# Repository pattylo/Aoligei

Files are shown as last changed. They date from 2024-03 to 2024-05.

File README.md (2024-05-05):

# AIRO-LAB Drone Standardization
## Aoligei-C, Aoligei-V, Aoligei-L

This documentation serves as the tutorial for setting up (from hardware to software) drone **Aoligei**, including -C (for control), -V (for visual), -L (for LiDAR).

## 1. What to buy.
- Follow this [file](/documents/buy_hardware.docx) to buy all the things your need. 
- Use the files [here]() to order 3D models. 

## 2. VIM4 - the on board computer
This document provides detailed guidance of configuring VIM4. We assume that you have
- A VIM4
- A heat sink for VIM4
- A fan for VIM4
- A 512G SD card
- A stable WIFI connection
- A HDMI monitor
- A set of external keyboard and mouse

### 2.1. Install Ubuntu 22.04 to VIM4
1.  Install the heatsink and the fan to VIM4 by following the manual provided in the heatsink package. VIM4 does not work without a heatsink.

2. Insert the SD card into a SD card reader.

3. Download the software from https://docs.khadas.com/products/sbc/vim4/install-os/install-os-into-external-storage, and download “ETCHER FOR WINDOWS (X86|X64) (INSTALLER)”.

4. Download the system image from https://dl.khadas.com/products/vim4/firmware/ubuntu/generic/. Choose “vim4-ubuntu-22.04-gnome-linux-5.15-fenix-1.6-231229.img.xz”.

5. Use the software “balenaEtcher” and the system image downloaded in Step2 to install ubuntu for VIM4.

### 2.2. Post Installation
1. First setup a new username with [NATO-alphabets](https://en.wikipedia.org/wiki/NATO_phonetic_alphabet) (for easy management lah...). Make it administrator to have ```sudo``` power. 
2. Then, reboot, login with new user, and delete the ```khadas``` user. Run the following to change the username:
    ```
    sudo passwd {username}
    ```
3. For convenience, you'd better install Firefox to your VIM4 because Google Chrome is not supported.

`However, YOU MUST NOT USE "snap" to install Firefox since there might be a bug in arm-ubuntu22.04. 
 Therefore, either install Firefox with traditional "apt-get" or do not use Firefox !!`

4. Install docker in VIM4. Follow this [page](https://docs.docker.com/engine/install/ubuntu/) and it should get the task done. Remember to read everything when you are doing the installation, please do not just blindly copy every single command into your terminal.
5. Do the following to get your Docker image:
    ```
    git clone https://github.com/HKPolyU-UAV/airo_docker_lib
    ./build_hehe.sh vimswift
    ```
   After building the image, do:
   ```
   ./run_hehe.sh vimswift
   ```
6. Voila! You have an usable programming environment now! When modifying your code, we suggest you to use VScode on your own laptop and connect the drone with ```ssh```. You can refer to this [documentation](https://github.com/pattylo/useful_tools/blob/main/vscode_github/vscode_github.md) for more info.

## 3. Firmware Setup
- A computer w/ Ubuntu >=20.04
- A Kakute FCU (v1.3 || v2)
- A Type-C USB wire
- A 4G SD card (if you are using Kakute v1.3)

### 3.1. Firmware Upgrade
1. Install DFU library on your own computer
    ```
    sudo apt install dfu-util -y
    ```
2. Erase and load the binary file to the FCU.
    ```
    git clone https://github.com/HKPolyU-UAV/Aoligei.git && cd Aoligei
    ```
    Then, unplug your USB connection, press the DUF button, plug your FCU into your computer, and unpress the DFU button. Then, do:
    ```
    dfu-util -a 0 --dfuse-address 0x08000000:force:mass-erase:leave -D ./build/holybro_kakuteh7_bootloader.bin 
    # ignore the error
    # use "holybro_kakuteh7v2_bootloader" if your are using v2
    ```
    And then, unplug your USB connection, press the DUF button, plug your FCU into your computer, and unpress the DFU button. Now do:
    ```
    dfu-util -a 0 --dfuse-address 0x08000000 -D ./build/holybro_kakuteh7_bootloader.bin
    # again, use "holybro_kakuteh7v2_bootloader" if your are using v2
    ```
3. Load firmware to the FCU. Open QGC, and go to "Firmware" to upload ```.px4``` to FCU. Note that you should tick on "advance settings", and then select "Custom firmware file..." under the drop-down options.

   <div align=center>
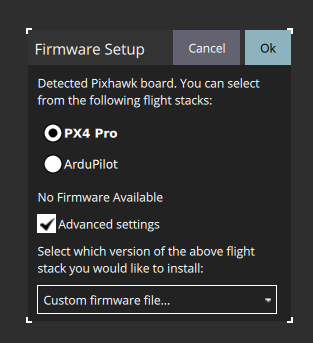
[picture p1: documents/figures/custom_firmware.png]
   
   </div>

    Click "OK", it should pop out a file selection panel. Go the "build" file of this repo, and select [this (v1.3)](/build/holybro_kakuteh7_default.px4) or [that (v2)](/build/holybro_kakuteh7v2_default.px4).

4. If you want to build from source on your own, refer to [this](./documents/fcu.md)

## 4. Pre-configuration of the FCU
### 4.1. Parameter settings
We assume you have at least finished the procedure "C" aforementioned. This part provides some pre-configurations of the FCU. Therefore, we assume you have

- An assembled drone with a FCU, a VIM4, four motors, a battery. (If you still don't know how to install ubuntu22 or docker file into VIM4, never mind. It won't affect this step.)
- QGC in Ubuntu. (Windows would be fine, but Ubuntu is preferred.)
- A type-C cable.

**NOTING: This drone is currently only used in a motion-capture-located in-door room. Out door flight is currently not supported.**

You may need half a minute to connect the FCU with QGC. When the connection is stable, you can see a content on the left of GQC.
Select "Parameters", and the following parameters need to be reset:

| Parameter |  Value | Comment |
|:---:|:---:|:---:|
| SYS_HAS_MAG | 0 |  This FCU does not have a magnetometer  |
| SYS_HAS_GPS | Disabled | This drone does not have a GPS |
| SYS_HAS_BARO | Disabled | This FCU does not have a barometer |
| SYS_MC_EST_GROUP | ekf2 | |
| SDLOG_MODE | disabled | Disable the log file to save CPU memory |

Reboot the FCU with QGC, when the FCU is reloaded, set

| Parameter |  Value | Comment |
|:---:|:---:|:---:|
|  EKF2_EV_CTRL  | 15 | |
|  EKF2_HGT_REF  |  Vision  | |
|  MAV_0_CONFIG  | Disabled | |
|  MAV_1_CONFIG  |  TELEM1  | |
| SER_TEL1_BAUD  |  921600  | |

Reboot the FCU with QGC, and this step is completed.

### 4.2. Quadrotor calibration
Then, we start to calibrate the quadrotor. Noting that different people have different styles.
Therefore, you don't need to follow EVERYTHING. We assume you can connect the FCU with QGC.

#### 4.2.1 Sensors
Calibrate Gyroscope, Accelerator, Level Horizon, and Orientations, respectively.
The "Autopilot Orientation" is "ROTATION_NONE" (default.)

#### 4.2.2. Radio
We need to connect the FASST receiver to the radio. Firstly, open the radio and switch it to FASST mode.
Secondly, push the mode select button on the receiver and then power on the receiver.
Now the light on the receiver is shinning and remains green. Then connection is finished.
We use "Mode2" here, as shown bellow. (If you have your own style, follow you own style.)

<div align=center>
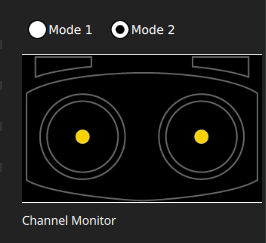
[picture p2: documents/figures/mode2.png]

</div>

Then, calibrate the radio as others do. Nothing special; therefore, detailed description is omitted here.

#### 4.2.3. Flight mode setting
The following is the mode setting of our group. You can have your own style.

<div align=center>
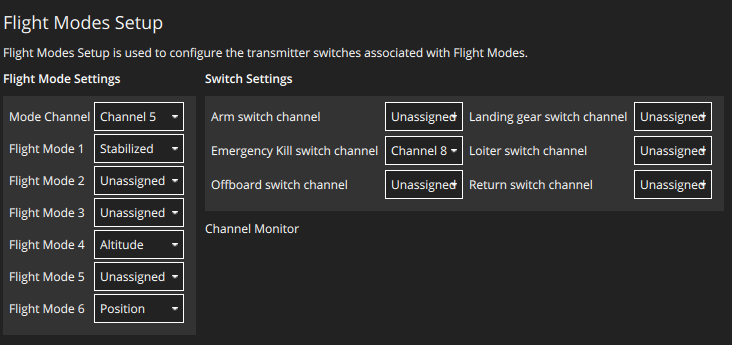
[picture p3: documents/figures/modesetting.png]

</div>

#### 4.2.4. Power setup and ESC calibration
**DO NOT INSTALL PROPELLERS!!**

Connect the drone with the battery. Push the first "Calculate" in the following figure.
Enter the measured voltage of the battery into the blank.
Then, and write the series of your battery (3, 4, or 6) into "Number of Cells"

<div align=center>
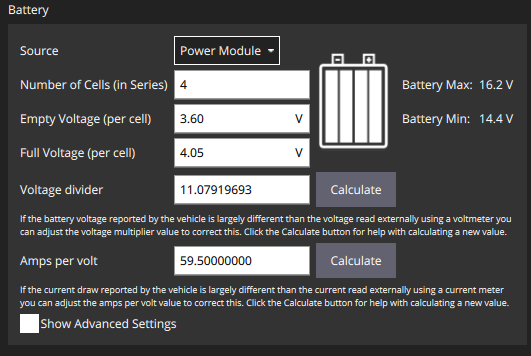
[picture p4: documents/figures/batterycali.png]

</div>

Then, calibrate the ESC. Click the button in the following figure. Just follow the instructions.
<div align=center>
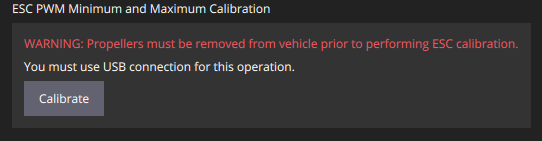
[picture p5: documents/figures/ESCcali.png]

</div>

#### 4.2.5. Calibrate Actuators
Firstly, you should see a screen like this.

<div align=center>
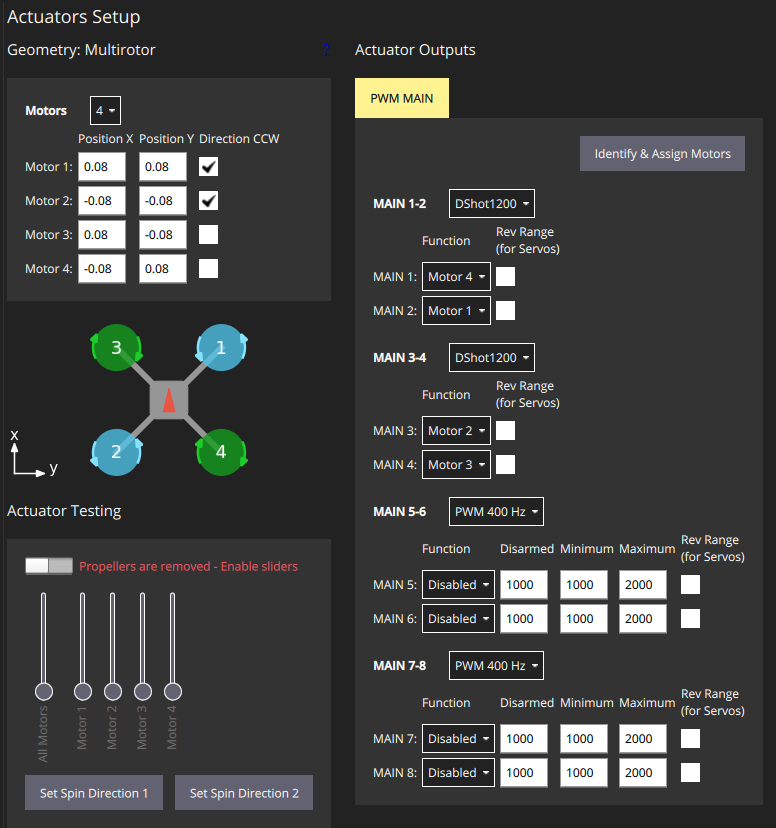
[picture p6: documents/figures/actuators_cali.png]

</div>

See the right column, set the MAIN1-2 and MAIN3-4 to "DShot1200", and then press "Identify & Assign Motors".

Secondly, see the left column, the positions (X and Y) from Motor 1 to 4 are shown below.

|  Motor |  Position X  |  Position Y  |  Direction CCW  |
|:---:|:---:|:---:|:---:|
|  Motor1  | 0.08 | 0.08 | Yes |
|  Motor2  | -0.08 | -0.08 | Yes |
|  Motor3  | 0.08 | -0.08 | No |
|  Motor4  | -0.08 | 0.08 | No |

Noting that the "0.08" here is especially designed for our own drone.
You'd better use a ruler to measure the semi-major axis of your own drone.
Then, the expected rotation direction of the four motors are shown in the QGC.

<div align=center>
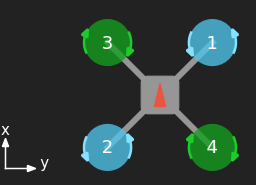
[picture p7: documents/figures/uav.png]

</div>

Finally, you need to reverse the rotation direction if some motors don't rotate as expected.
Use the buttons "Set Spin Direction 1" and "Set Spin Direction 2" to correct them, which are shown below.

<div align=center>
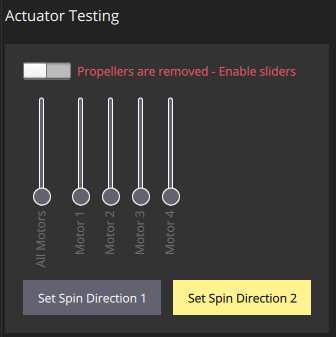
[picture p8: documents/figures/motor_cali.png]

</div>

### 4.3 Post Calibration
Unplug your SD card, connect the SD card to your PC. Create a new folder "etc" to the SD card.
create "extras.txt" in "etc" folder. Then, copy the following items into the txt file.

```
mavlink stream -d /dev/ttyS0 -s LOCAL_POSITION_NED -r 100
mavlink stream -d /dev/ttyS0 -s ATTITUDE_TARGET -r 100
mavlink stream -d /dev/ttyS0 -s BATTERY_STATUS -r 100
```

Congratulations! If everything goes well, you have finished pre-configurations of the drone.

`Tips: Although we provide detailed calibration instruction here,
many users (including ourselves) would meet many confused bugs while doing the step.
That is because different people have totally different styles, use different hardware, have different QGC version, have different radios, et al. 
PLease feel free to ask the "Maintainers" shown below and share us your weired bugs.
We might don't know how to fix your bugs, but we are curious about them. Thank you very much!`

## 5. System Identification 
@ https://github.com/RockyJBL
Please follow the [link](https://github.com/HKPolyU-UAV/airo_control_interface.git) here to conduct the system identification.

## Maintainers
[Yefeng](https://github.com/Yang-Yefeng) @ AIRO-LAB @ RCUAS, HKPolyU <br>
[RockyJBL](https://github.com/RockyJBL) @ AIRO-LAB @ RCUAS, HKPolyU <br>
[VITO](https://github.com/Vitollee) @ AIRO-LAB @ RCUAS, HKPolyU <br>
[pattylo](https://github.com/pattylo) @ AIRO-LAB @ RCUAS, HKPolyU

<!-- # PX4 Drone Autopilot

[![Releases](https://img.shields.io/github/release/PX4/PX4-Autopilot.svg)](https://github.com/PX4/PX4-Autopilot/releases) [![DOI](https://zenodo.org/badge/22634/PX4/PX4-Autopilot.svg)](https://zenodo.org/badge/latestdoi/22634/PX4/PX4-Autopilot)

[![Nuttx Targets](https://github.com/PX4/PX4-Autopilot/workflows/Nuttx%20Targets/badge.svg)](https://github.com/PX4/PX4-Autopilot/actions?query=workflow%3A%22Nuttx+Targets%22?branch=master) [![SITL Tests](https://github.com/PX4/PX4-Autopilot/workflows/SITL%20Tests/badge.svg?branch=master)](https://github.com/PX4/PX4-Autopilot/actions?query=workflow%3A%22SITL+Tests%22)

[![Discord Shield](https://discordapp.com/api/guilds/1022170275984457759/widget.png?style=shield)](https://discord.gg/dronecode)

This repository holds the [PX4](http://px4.io) flight control solution for drones, with the main applications located in the [src/modules](https://github.com/PX4/PX4-Autopilot/tree/main/src/modules) directory. It also contains the PX4 Drone Middleware Platform, which provides drivers and middleware to run drones.

PX4 is highly portable, OS-independent and supports Linux, NuttX and MacOS out of the box.

* Official Website: http://px4.io (License: BSD 3-clause, [LICENSE](https://github.com/PX4/PX4-Autopilot/blob/main/LICENSE))
* [Supported airframes](https://docs.px4.io/main/en/airframes/airframe_reference.html) ([portfolio](https://px4.io/ecosystem/commercial-systems/)):
  * [Multicopters](https://docs.px4.io/main/en/frames_multicopter/)
  * [Fixed wing](https://docs.px4.io/main/en/frames_plane/)
  * [VTOL](https://docs.px4.io/main/en/frames_vtol/)
  * [Autogyro](https://docs.px4.io/main/en/frames_autogyro/)
  * [Rover](https://docs.px4.io/main/en/frames_rover/)
  * many more experimental types (Blimps, Boats, Submarines, High altitud Pe balloons, etc)
* Releases: [Downloads](https://github.com/PX4/PX4-Autopilot/releases)

## Building a PX4 based drone, rover, boat or robot

The [PX4 User Guide](https://docs.px4.io/main/en/) explains how to assemble [supported vehicles](https://docs.px4.io/main/en/airframes/airframe_reference.html) and fly drones with PX4.
See the [forum and chat](https://docs.px4.io/main/en/#getting-help) if you need help!

## Changing code and contributing

This [Developer Guide](https://docs.px4.io/main/en/development/development.html) is for software developers who want to modify the flight stack and middleware (e.g. to add new flight modes), hardware integrators who want to support new flight controller boards and peripherals, and anyone who wants to get PX4 working on a new (unsupported) airframe/vehicle.

Developers should read the [Guide for Contributions](https://docs.px4.io/main/en/contribute/).
See the [forum and chat](https://docs.px4.io/main/en/#getting-help) if you need help!

### Weekly Dev Call

The PX4 Dev Team syncs up on a [weekly dev call](https://docs.px4.io/main/en/contribute/).

> **Note** The dev call is open to all interested developers (not just the core dev team). This is a great opportunity to meet the team and contribute to the ongoing development of the platform. It includes a QA session for newcomers. All regular calls are listed in the [Dronecode calendar](https://www.dronecode.org/calendar/).

## Maintenance Team

Note: This is the source of truth for the active maintainers of PX4 ecosystem.

| Sector | Maintainer |
|---|---|
| Founder | [Lorenz Meier](https://github.com/LorenzMeier) |
| Architecture | [Daniel Agar](https://github.com/dagar) / [Beat Küng](https://github.com/bkueng)|
| State Estimation | [Mathieu Bresciani](https://github.com/bresch) / [Paul Riseborough](https://github.com/priseborough) |
| OS/NuttX | [David Sidrane](https://github.com/davids5) |
| Drivers | [Daniel Agar](https://github.com/dagar) |
| Simulation | [Jaeyoung Lim](https://github.com/Jaeyoung-Lim) |
| ROS2 | [Beniamino Pozzan](https://github.com/beniaminopozzan) |
| Community QnA Call | [Ramon Roche](https://github.com/mrpollo) |
| [Documentation](https://docs.px4.io/main/en/) | [Hamish Willee](https://github.com/hamishwillee) |

| Vehicle Type | Maintainer |
|---|---|
| Multirotor | [Matthias Grob](https://github.com/MaEtUgR) |
| Fixed Wing | [Thomas Stastny](https://github.com/tstastny) |
| Hybrid VTOL | [Silvan Fuhrer](https://github.com/sfuhrer) |
| Boat | x |
| Rover | x |

See also [maintainers list](https://px4.io/community/maintainers/) (px4.io) and the [contributors list](https://github.com/PX4/PX4-Autopilot/graphs/contributors) (Github). However it may be not up to date.

## Supported Hardware

Pixhawk standard boards and proprietary boards are shown below (discontinued boards aren't listed).

For the most up to date information, please visit [PX4 user Guide > Autopilot Hardware](https://docs.px4.io/main/en/flight_controller/).

### Pixhawk Standard Boards

These boards fully comply with Pixhawk Standard, and are maintained by the PX4-Autopilot maintainers and Dronecode team

* FMUv6X and FMUv6C
  * [CUAV Pixahwk V6X (FMUv6X)](https://docs.px4.io/main/en/flight_controller/cuav_pixhawk_v6x.html)
  * [Holybro Pixhawk 6X (FMUv6X)](https://docs.px4.io/main/en/flight_controller/pixhawk6x.html)
  * [Holybro Pixhawk 6C (FMUv6C)](https://docs.px4.io/main/en/flight_controller/pixhawk6c.html)
  * [Holybro Pix32 v6 (FMUv6C)](https://docs.px4.io/main/en/flight_controller/holybro_pix32_v6.html)
* FMUv5 and FMUv5X (STM32F7, 2019/20)
  * [Pixhawk 4 (FMUv5)](https://docs.px4.io/main/en/flight_controller/pixhawk4.html)
  * [Pixhawk 4 mini (FMUv5)](https://docs.px4.io/main/en/flight_controller/pixhawk4_mini.html)
  * [CUAV V5+ (FMUv5)](https://docs.px4.io/main/en/flight_controller/cuav_v5_plus.html)
  * [CUAV V5 nano (FMUv5)](https://docs.px4.io/main/en/flight_controller/cuav_v5_nano.html)
  * [Auterion Skynode (FMUv5X)](https://docs.auterion.com/avionics/skynode)
* FMUv4 (STM32F4, 2015)
  * [Pixracer](https://docs.px4.io/main/en/flight_controller/pixracer.html)
  * [Pixhawk 3 Pro](https://docs.px4.io/main/en/flight_controller/pixhawk3_pro.html)
* FMUv3 (STM32F4, 2014)
  * [Pixhawk 2](https://docs.px4.io/main/en/flight_controller/pixhawk-2.html)
  * [Pixhawk Mini](https://docs.px4.io/main/en/flight_controller/pixhawk_mini.html)
  * [CUAV Pixhack v3](https://docs.px4.io/main/en/flight_controller/pixhack_v3.html)
* FMUv2 (STM32F4, 2013)
  * [Pixhawk](https://docs.px4.io/main/en/flight_controller/pixhawk.html)

### Manufacturer supported

These boards are maintained to be compatible with PX4-Autopilot by the Manufacturers.

* [ARK Electronics ARKV6X](https://docs.px4.io/main/en/flight_controller/arkv6x.html)
* [CubePilot Cube Orange+](https://docs.px4.io/main/en/flight_controller/cubepilot_cube_orangeplus.html)
* [CubePilot Cube Orange](https://docs.px4.io/main/en/flight_controller/cubepilot_cube_orange.html)
* [CubePilot Cube Yellow](https://docs.px4.io/main/en/flight_controller/cubepilot_cube_yellow.html)
* [Holybro Durandal](https://docs.px4.io/main/en/flight_controller/durandal.html)
* [Airmind MindPX V2.8](http://www.mindpx.net/assets/accessories/UserGuide_MindPX.pdf)
* [Airmind MindRacer V1.2](http://mindpx.net/assets/accessories/mindracer_user_guide_v1.2.pdf)
* [Holybro Kakute F7](https://docs.px4.io/main/en/flight_controller/kakutef7.html)

### Community supported

These boards don't fully comply industry standards, and thus is solely maintained by the PX4 public community members.

### Experimental

These boards are nor maintained by PX4 team nor Manufacturer, and is not guaranteed to be compatible with up to date PX4 releases.

* [Raspberry PI with Navio 2](https://docs.px4.io/main/en/flight_controller/raspberry_pi_navio2.html)
* [Bitcraze Crazyflie 2.0](https://docs.px4.io/main/en/complete_vehicles/crazyflie2.html)

## Project Roadmap

**Note: Outdated**

A high level project roadmap is available [here](https://github.com/orgs/PX4/projects/25).

## Project Governance

The PX4 Autopilot project including all of its trademarks is hosted under [Dronecode](https://www.dronecode.org/), part of the Linux Foundation.

<a href="https://www.dronecode.org/" style="padding:20px" ><img src="https://mavlink.io/assets/site/logo_dronecode.png" alt="Dronecode Logo" width="110px"/></a>
<a href="https://www.linuxfoundation.org/projects" style="padding:20px;"><img src="https://mavlink.io/assets/site/logo_linux_foundation.png" alt="Linux Foundation Logo" width="80px" /></a>
<div style="padding:10px">&nbsp;</div> -->

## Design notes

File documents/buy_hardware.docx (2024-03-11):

物品 | 数量 | 链接 | 备注 | 价格 (大约\RMB)
飞控板 (电调) | 1个 | 【淘宝】https://m.tb.cn/h.5ve4uwALOcqdL18?tk=eCySWmf9DYx CZ0012 「Holybro Kakute H7 V1.3 飞控 F7 大疆 模拟 航模 蓝牙」 点击链接直接打开 或者 淘宝搜索直接打开 | H7 V1.3+Tekko32 F4 4in1 50A ESC | 1100
飞控板SD卡 | 1张 | 【淘宝】https://m.tb.cn/h.5ECz1sldd7Osilm?tk=vJC2Wmf7vUz CZ8908 「sandisk闪迪tf卡4g手机内存卡class4存储卡micro sd卡小音箱 小卡」 点击链接直接打开 或者 淘宝搜索直接打开 | 4G | 30
板载计算机 | 1台 | 【淘宝】https://m.tb.cn/h.5vIIDjsSOScYAkE?tk=z8ViWmfkVCp CZ0002 「khadas VIM4 Amlogic A311D2 开发板Mali G52 MP8(8EE) GPU」 点击链接直接打开 或者 淘宝搜索直接打开 | Khadas VIM4 + 散热器 + 风扇 | 1650
板载计算机SD卡 | 1张 | 【淘宝】https://m.tb.cn/h.5ve4uzfCTN9hk0G?tk=zud9Wmf9DXo CZ8908 「三星TF卡512G存储卡手机电脑平板摄像头记录仪无人机switch内存卡」 点击链接直接打开 或者 淘宝搜索直接打开 | 512G PRO Plus | 350
航模电机 | 4个 | 【淘宝】https://m.tb.cn/h.5ve4F0b5MVgFCnf?tk=xtZvWmf7v6d CA6496 「T-Motor 乘风 Velox V2306 V2207 V2 电机 5寸 4S 6S 马达」 点击链接直接打开 或者 淘宝搜索直接打开 | V2207 KV1750 (V3.0) | 300 (4个)
电池 | 1块 | 【淘宝】https://m.tb.cn/h.5ve4uzAfdkGmNAv?tk=uTMPWmf9DXz HU9046 「ACE格氏4S电池 航模 5300 4000 3300 2600 2200MAH 格式14.8V锂电」 点击链接直接打开 或者 淘宝搜索直接打开 | 4S 2700 mAh，如果没有，2400mAh或者3300mAh也行 | 300
机架 | 1套 | 无 | 李凡一1.0 | 200
FASST 接收机 | 1个 | 【淘宝】https://m.tb.cn/h.5EyjOM2?tk=CumVWmf5fD0 CZ0000 「X-BOSS FM900接收机 RSSI输出 FASST协议 穿越机SBUS/FUTABA/2.4G」 点击链接直接打开 或者 淘宝搜索直接打开 | FASST | 90
航模遥控器 | 1个 | 【淘宝】https://m.tb.cn/h.5vVZYqGZzLXjnPT?tk=mNvEWmU8Bd0 CZ0001 「FUTABA T16IZS SUPER 香槟金版本18通遥控器中文菜单16IZ升级」 点击链接直接打开 或者 淘宝搜索直接打开 | 左手油门/美国手 | 3200
升压模块 | 1个 | 【淘宝】https://m.tb.cn/h.5EeQpN7h2WZBn2v?tk=xdZbWmfUERN CZ3458 「DC-DC升压模块 SX1308可调升压模块/2A升压板 带MICRO/2A升压板」 点击链接直接打开 或者 淘宝搜索直接打开 | 看好升压范围，输出能囊括12-20V即可 | 3
USB转串口TTL | 1个 | 【淘宝】https://m.tb.cn/h.5w9Yb4wYnox8S4l?tk=wyDZWmHhYEv MF1643 「CP2102模块USB转TTL升级板UBS转串口STC单片机下载刷机六合一UART」 点击链接直接打开 或者 淘宝搜索直接打开 | CP2102版 | 25
螺旋桨 | 1套 | 【淘宝】https://m.tb.cn/h.5ECJTSyQdFe4Gub?tk=SixTWmf7vgv CZ0001 「乾丰MCK 51466V2 5寸穿越机FPV竞速桨叶 51466V2 5寸竞速螺旋桨」 点击链接直接打开 或者 淘宝搜索直接打开 | 1套=4个=正反各一对 2.5寸 51446 | 15
夜航灯 | 2套 | 【淘宝】https://m.tb.cn/h.5vIIDIuUUYiKGTO?tk=hrZpWmUWTFC HU0025 「F450夜航灯LED高亮多轴穿越机无人机航模多旋翼550探照灯七彩爆闪」 点击链接直接打开 或者 淘宝搜索直接打开 | 绿色，一个电路板，两个灯，一对导线 | 5 (2套)
夜航灯LED | 2套 | 【淘宝】https://m.tb.cn/h.5vIUZrr?tk=aQflWmfhbLB CZ0015 「0.5W 0.2W高亮5730冷白色LED贴片灯珠正白光暖白色蓝翠绿色黄红光」 点击链接直接打开 或者 淘宝搜索直接打开 | 红色灯珠 + LED底板 | 5 (若干)
M3隔离铜柱 | 4个 | 【淘宝】https://m.tb.cn/h.5EyQDMN?tk=A5JvWmf6ZU1 MF3543 「铝合金螺母柱隔离柱多轴无人机架圆形铝柱m3联接柱M3-D5D6多彩色」 点击链接直接打开 或者 淘宝搜索直接打开 | 18mm-22mm | 30 (若干)
M3 六角螺柱 | 4个 | 【淘宝】https://m.tb.cn/h.5veaiEd?tk=LC1tWmfhKZI HU7632 「不锈钢单头六角螺柱机箱主板连接柱隔离柱铜柱螺丝柱M2M3M4M5M6M8」 点击链接直接打开 或者 淘宝搜索直接打开 | M3*3+6 – M3*5+6 | 20 (若干)
电池减震垫 | 1个 | 【淘宝】https://m.tb.cn/h.5vsbync55OhF4NI?tk=ZwnsWmGFvgl HU7632 「丨兄弟连模型穿越机电池保护板花牌格式锂航模机架配件碳纤维板」 点击链接直接打开 或者 淘宝搜索直接打开 | 95*45*1.5 (带胶) | 25

备注：

- 每一架无人机 (不含遥控器) 成本约为：1100 + 30 + 1650 + 350 + 300 + 300 + 200 + 3 + 25 + 15 + 5 + 5 + 90 + 30 + 20 + 25 = 4148 (RMB) ≈ 4200 (RMB)
- 每一架无人机 (含遥控器) 成本约为：4200 + 3200 = 7500 (RMB)
- 所提供链接为手机链接，电脑访问只需要复制所提供链接里面的网址即可
- 除所列出项目之外，还有一些耗材 (导线，螺母，焊锡等) 无法计数，如有需要自行购买即可

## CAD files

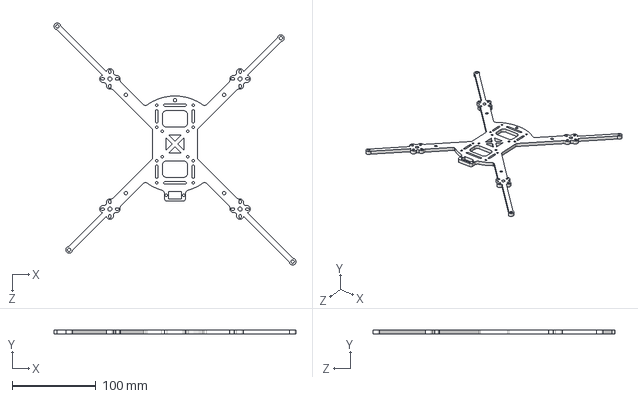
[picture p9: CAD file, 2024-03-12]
3D_models/C/airframe_R6.STEP
289.3 x 5.00 x 289.3 mm

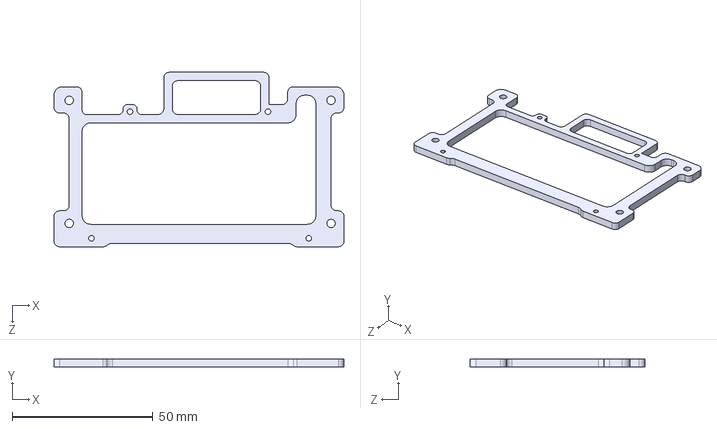
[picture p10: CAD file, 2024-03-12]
3D_models/V/vim4_mount.STEP
103.0 x 3.00 x 62.0 mm

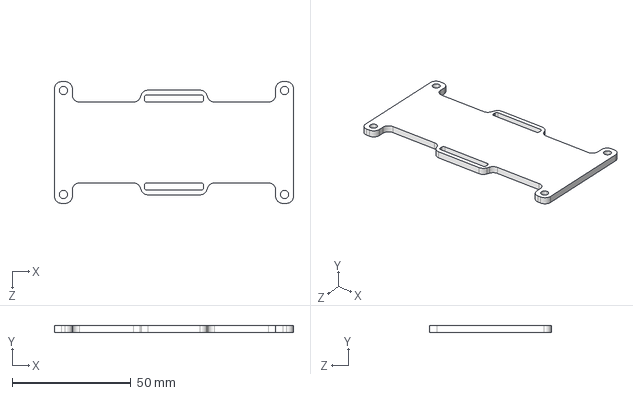
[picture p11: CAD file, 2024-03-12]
3D_models/C/battey_adopat_P2.STEP
100.5 x 3.00 x 51.2 mm

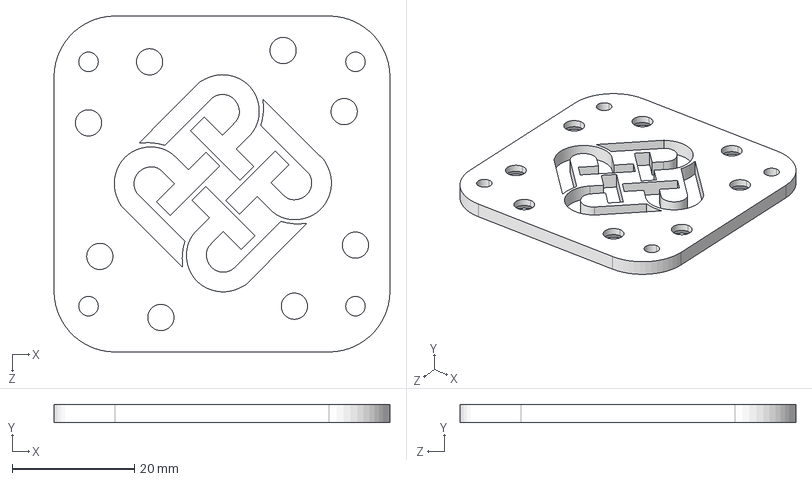
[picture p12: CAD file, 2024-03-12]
3D_models/C/cover_R3.STEP
55.0 x 3.00 x 55.0 mm

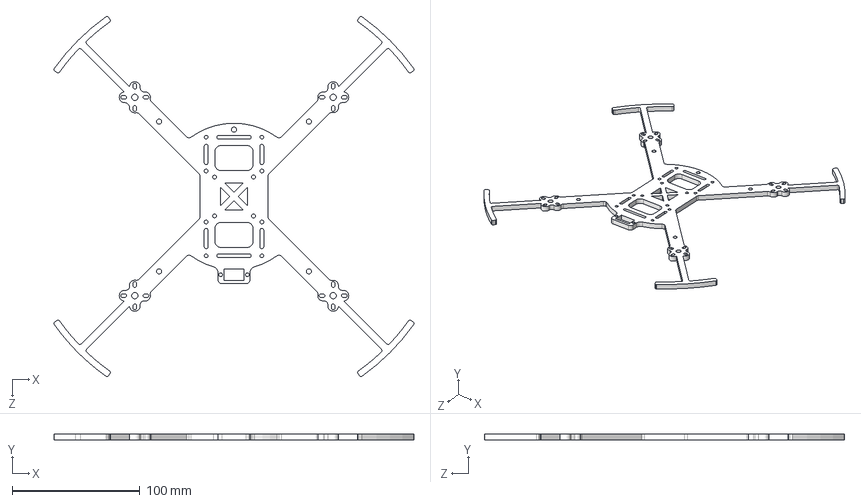
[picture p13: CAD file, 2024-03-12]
3D_models/V/airframe.STEP
282.3 x 5.00 x 282.3 mm

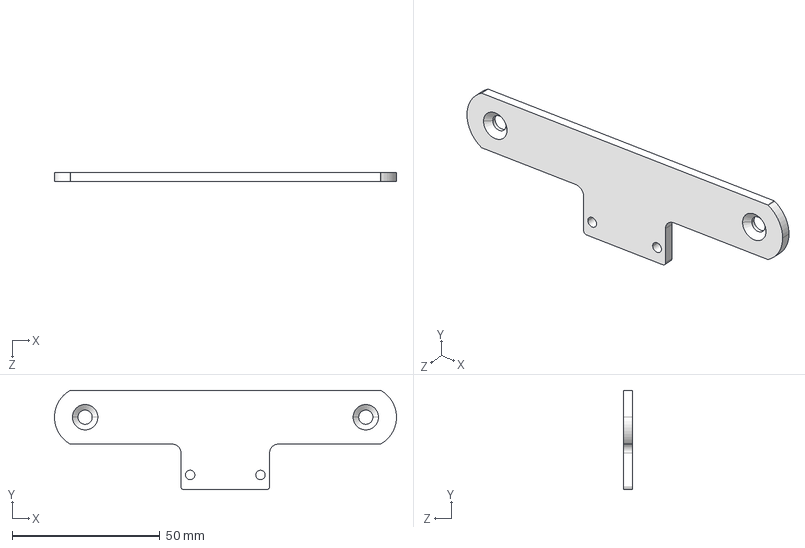
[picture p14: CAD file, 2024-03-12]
3D_models/V/D455C_adopter.STEP
115.8 x 33.6 x 3.00 mm

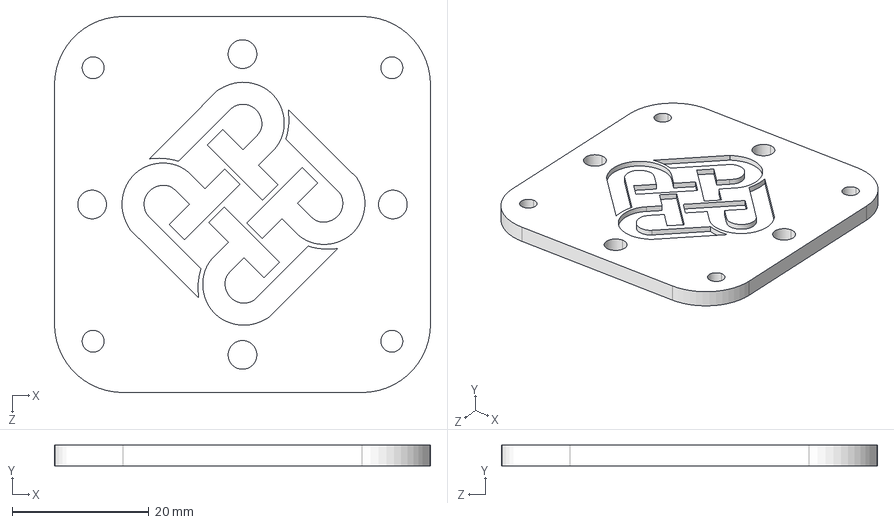
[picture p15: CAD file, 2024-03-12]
3D_models/V/cover.STEP
55.0 x 3.00 x 55.0 mm

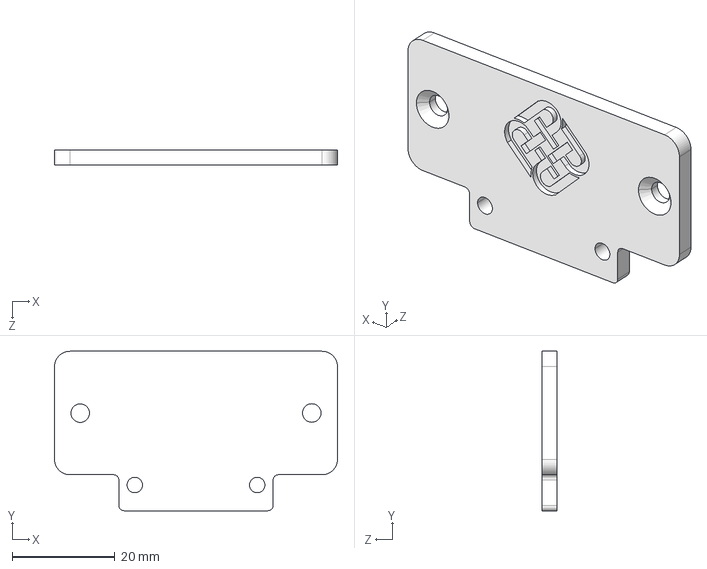
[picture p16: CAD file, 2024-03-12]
3D_models/V/D435i_adopter.STEP
55.0 x 31.0 x 3.00 mm

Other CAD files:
3D_models/V/battey_adopat.STEP

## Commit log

2024-03-12 add 3D models
    [D435i_adopter.STEP, D455C_adopter.STEP, airframe.STEP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]
2024-03-12 干他就完了
2024-03-12 奥利给干他就完了
